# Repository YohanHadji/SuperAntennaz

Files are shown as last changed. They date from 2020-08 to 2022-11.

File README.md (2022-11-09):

# SuperAntennaz

### Introduction 

SuperAntennaz is an antenna rotator designed for satellite traking. 

It can support more than 10kg of antenna, orientate them really fast (close to 30 deg. /s) and in its final version, it is very simple to reproduce. It is therefore perfect to be built, modified, and improved by the community of space HAM enthusiasts all over the world.

### Content 
- [Specifications](#Specifications)
- [Presentation](#Presentation)
- [Part List](#Part-List)
- [Kit production and prices](#Kit-production-and-prices)

## Specifications

Max torque - Min. 60 Nm

Max speed  - 30°/s 

Weight     ~ 5.5kg

Outdorproof - YES 

## Presentation

You can vizualise the rotator in 3D online with this link : https://a360.co/2CAJL9K 

This is a render of the last version prototype :

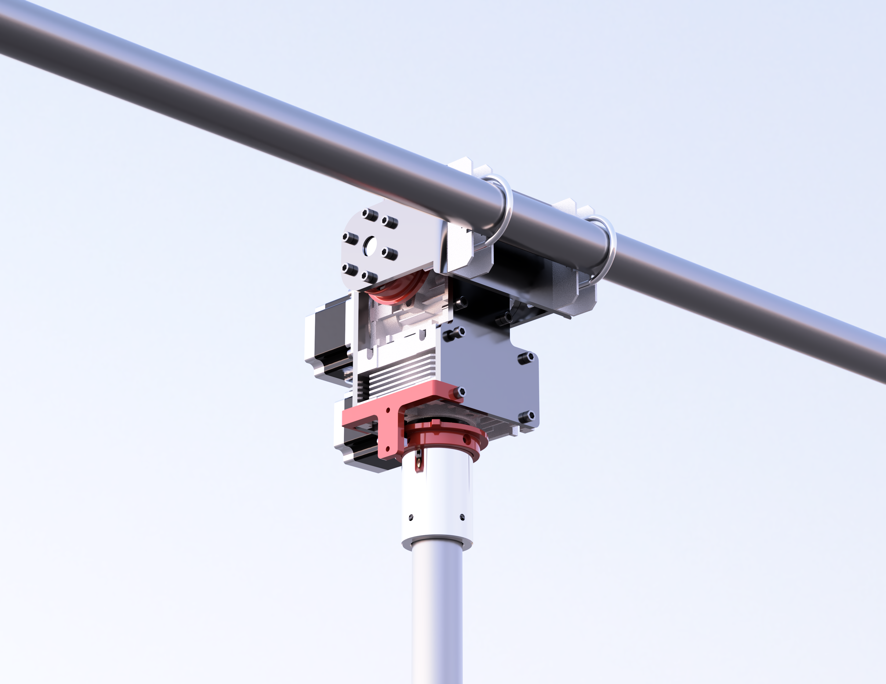
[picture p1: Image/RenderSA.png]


These are (real!) pictures of the latest version : 

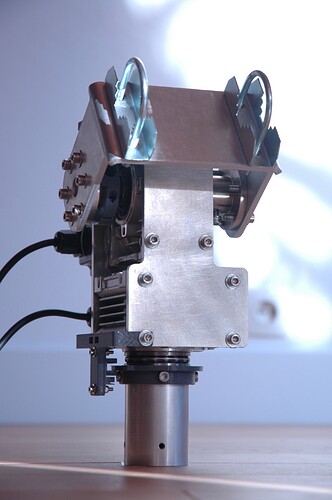
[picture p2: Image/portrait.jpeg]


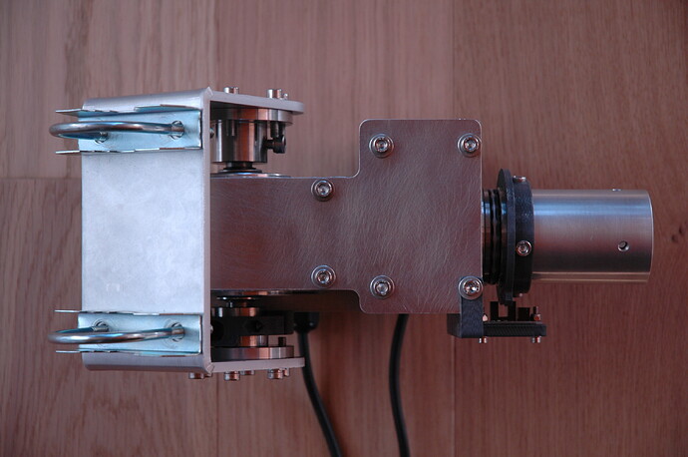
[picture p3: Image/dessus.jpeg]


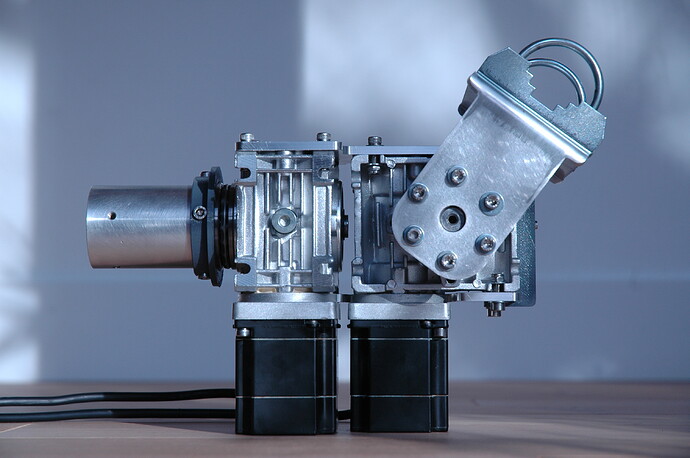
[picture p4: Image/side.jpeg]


This is a picture of a previous version of the rotator mounted on a roof with its mast, its antenna, and its creator :) 

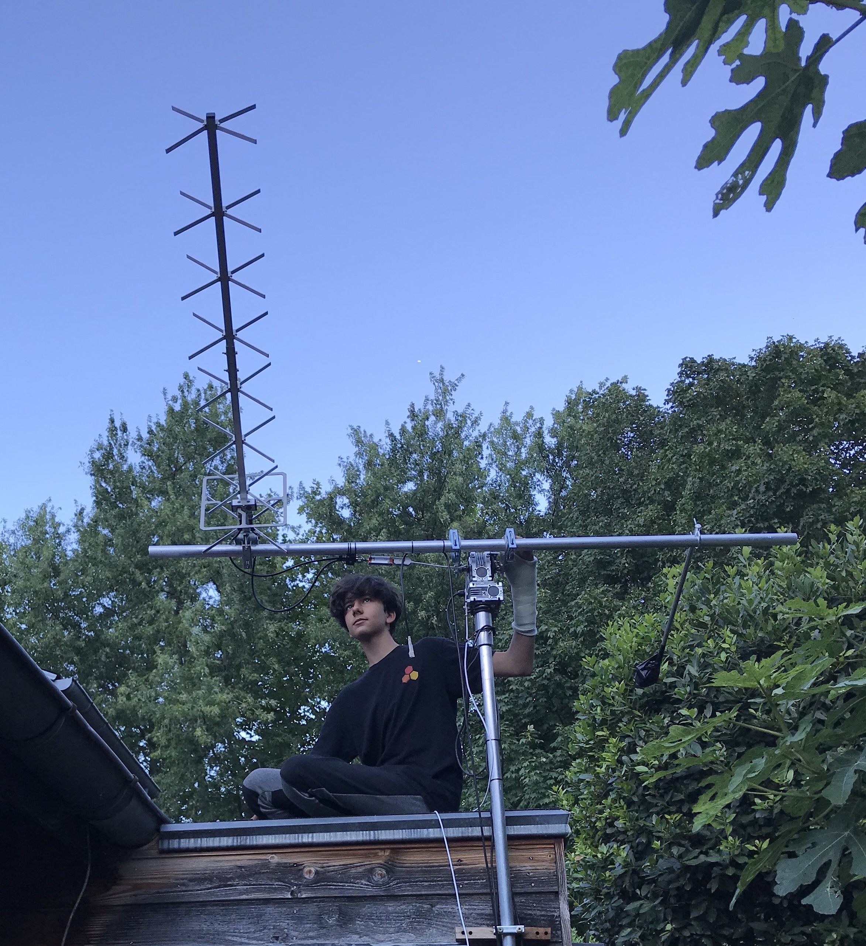
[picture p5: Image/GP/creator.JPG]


You can see the rotator in action in this video : https://www.youtube.com/watch?v=NuH7F1J6nr8

## Part List

1/ Mechanical parts on the market

- 2 * RV030 Worm Gear Reducer https://fr.aliexpress.com/item/4000405892097.html - 30€
- 2 * Reducer shaft adapatator https://fr.aliexpress.com/item/4000430356079.html - 5€
- 2 * Waterproof Stepper Motor https://www.omc-stepperonline.com/waterproof-stepper-motor/p-series-ip65-waterproof-nema-23-stepper-motor-4-0a-1-2nm-169-97oz-in.html - 80€
- 2 * 14 mm Key Hub (connection between the elevation axis and the bracket) https://ozrobotics.com/shop/14mm-stainless-steel-key-hub-18014/ - 40€
- 1 * 14 mm simple reducer shaft https://fr.aliexpress.com/item/4000378786811.html - 8€
- 1 * 14 mm double reducer shaft https://fr.aliexpress.com/item/4000378899246.html - 10€
- 2 * 50 mm mast jaws https://www.mhzshop.com/shop/Accessoires-MHz/Fixations/Brides/Bride-pour-tube-40mm.html 5€ 
- 2 * Optical Endstop - 5€ 
- ~20 * M5 screw & nut - 8€ 
- ~20 * M4 screw & nut - 8€ 

  Total = 21 parts, ~ 200€ 

2/ Machined part,(price is for part ordered one by one)

- 1 * Alumnium Mast Mount 80€
- 1 * Bracket 80€
- 1 * Reducer alumnium plate mount 30€ 

- 1 * 3D printed elevation endstop mount and pin 5€ 
- 1 * 3D printed azimuth endstop mount and pin 5€

  Sub Total = 200€ 
  
 3/ Operation Parts 

- 1 * Arduino controller ~ 20€
- 2 * Stepper Drivers ~ 100€ 
- 1 * 300W Power supply ~ 30€
- 2 * 35 mm Mast (1,5m minimum) ~ 40€ 

  Sub Total = 190€ 

Grand Total : 
~ 600 € - for a fully operational rotator 
~ 500 € - for a rotator without control electronics and mast 
       
Note : An additional cost of 100€ is to be expected for all shipping costs. 

## Kit production and prices

If you are interested by the rotator but not sure about what to buy, I could purpose the following purchase options : 

NOT-AVAILABLE RIGHT NOW - Machined parts kit, contains : Machined parts, needed screw and nuts, building instruction. - 219€ + Shipping costs (~20€ for europe)

## How to ~not~ purchase 

Kits have been available at some point in the past, but I can't find the time right now to produce some anymore. Machining prices also went high and local supplier was asking for higher order volumes. I can still try to help you at hadji.[myname]@gmail.com.

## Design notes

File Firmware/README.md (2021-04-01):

# SatNOGS Rotator Firmware for Arduino UNO/CNC Shield, for DIRECT CONNECTION TO PC via serial

Firmware [SatNOGS Rotator Controller Based on Arduino UNO and CNC V3 Shield](https://wiki.satnogs.org/SatNOGS_Arduino_Uno/CNC_Shield_Based_Rotator_Controller).

Repository includes all source files for the SatNOGS rotator controller Firmware, based on the Arduino UNO. using the CNC v3 Shield, instead of the custom SatNOGS PCB.

Electronics can be found on [satnogs-rotator-controller](https://wiki.satnogs.org/SatNOGS_Arduino_Uno/CNC_Shield_Based_Rotator_Controller)

## Instructions

In order to use this code, you need to install
 * Arduino IDE
 * [AccelStepper library](http://www.airspayce.com/mikem/arduino/AccelStepper/index.html)
 * [PID_v1 library](https://github.com/br3ttb/Arduino-PID-Library)
 * Wire library
 * Gpredict

## Easycomm implemantation

* AZ, Azimuth, number - 1 decimal place [deg]
* EL, Elevation, number - 1 decimal place [deg]
* SA, Stop azimuth moving
* SE, Stop elevation moving
* RESET, Move to home position
* PARK, Move to park position
* IP, Read an input, number
    * Temperature = 0
    * SW1 = 1
    * SW2 = 2
    * Encoder1 = 3
    * Encoder2 = 4
    * Load of M1/AZ = 5
    * Load of M2/EL = 6
    * Speed of M1/AZ (DPS) = 7
    * Speed of M2/EL (DPS) = 8
* VE, Request Version
* GS, Get status register, number
    * idle = 1
    * moving = 2
    * pointing = 4
    * error = 8
* GE, Get error register, number
    * no_error = 1
    * sensor_error = 2
    * homing_error = 4
    * motor_error = 8
    * over_temperature = 12
    * wdt_error = 16
* VL, Velocity Left ,number [mdeg/s]
* VR, Velocity Right, number [mdeg/s]
* VU, Velocity Up, number [mdeg/s]
* VD, Velocity Down, number [mdeg/s]
* CR, Read config, register [0-x]
    * Gain P for M1/AZ = 1
    * Gain I for M1/AZ = 2
    * Gain D for M1/AZ = 3
    * Gain P for M2/EL = 4
    * Gain I for M2/EL = 5
    * Gain D for M2/EL = 6
    * Azimuth park position = 7
    * Elevation park position = 8
    * Control mode (position = 0, speed = 1) = 9
* CW, Write config, register [0-x]
    * Gain P for M1/AZ = 1
    * Gain I for M1/AZ = 2
    * Gain D for M1/AZ = 3
    * Gain P for M2/EL = 4
    * Gain I for M2/EL = 5
    * Gain D for M2/EL = 6
    * Azimuth park position = 7
    * Elevation park position = 8
    * This reg is set from Vx commands control mode (position = 0, speed = 1) = 9
* RB, custom command to reboot controller

## Controller Configurations

* Stepper Motor
    * Endstops
    * Encoders, optional
    * UART or R485 (For both options the firmware is the same)

## Pins Configuration

```
   #ifndef ROTATOR_PINS_H_
   #define ROTATOR_PINS_H_
   //#define M1IN1 10 ///< Motor 1 PWM pin
   #define M1IN1 2 ///< Motor 1 PWM pin
   #define M1IN2 5  ///< Motor 1 PWM pin
   #define M1SF  7  ///< Motor 1 digital input, status flag for DC Motor Drivers
   #define M1FB  A1 ///< Motor 1 analog input, current/load feedback for DC Motor Drivers
   #define M2IN1 3 ///< Motor 2 PWM pin
   #define M2IN2 6  ///< Motor 2 PWM pin
   #define M2SF  7 ///< Motor 2 digital input, status flag for DC Motor Drivers
   #define M2FB  A0 ///< Motor 2 analog input, current/load feedback for DC Motor Drivers
   #define MOTOR_EN 8 ///< Digital output, to enable the motors
   #define SW1 11 ///< Digital input, to read the status of end-stop for motor 1
   #define SW2 9 ///< Digital input, to read the status of end-stop for motor 2
   #define RS485_DIR 2 ///< Digital output, to set the direction of RS485 communication
   #define SDA_PIN 3 ///< I2C data pin
   #define SCL_PIN 4 ///< I2C clock pin
   #define PIN12 12 ///< General purpose I/O pin
   #define PIN13 13 ///< General purpose I/O pin
   #define A2    A2 ///< General purpose I/O & analog pin
   #define A3    A3 ///< General purpose I/O & analog pin
   #endif /* ROTATOR_PINS_H_ */
```

## Testing with hamlib - rotctl or with Serial Monitor

Software to install
Final pieces to the preparation work are to install a couple of pieces of software. firstly Hamlib. This will be used to communicate between GPredict and the Arduino. Secondly we will install the main prediction software, GPredict. We will not be going into detail about setup of GPredict but assume that you have followed the installation guide and had a play around with it so you can understand what it is and how it works.

Install hamlib

Download the Hamblib software and follow the installation process. this may require you installing it with Administrator rights. using device manager find the port for the Arduino, for the purposes of this we will assume it is COM7

Using a text editor, like Notepad++, to create a file with the code below in it. Note where COM7 is and amend with your own COM port. Save as a batch file (i.e. with th extension .bat file in the same folder as rotctld (Usually found in C:\Program Files (x86)\hamlib-w64-3.2\bin )

rotctld -m 202 -r COM7 -s 9600 -T 127.0.0.1 -t 4533 -C timeout=500 -C retry=0 -vvvvvvvv > pause
Install GPredict

Download and install GPredict. Next we will need to add a rotator. Go to Edit > Preferences > Interfaces > Rotators > Add New

Give it a name. For example Arduino. The port is localhost 4533

That's it for setup. next we will test the system

Testing
We will need to do a few things to get the system running.

Start the .bat file
In GPredict open up the Antenna module and click Engage
You should see that in the batch file output a series of commands being sent to the Arduino
Check that both the Az and Ele work correctly by manually driving the rotator
Occasionally this might not work first time. A restart of both hamlib and Gpredict worked

Tweaks
There is a huge variety in parts that can get bought, here are a few tweaks that may be necessary.

Motors are turning the wrong way - This may need the pins checking

It is only moving half the distance - Change the gear ratio in the main sketch

The limit switches are not working - Change the following code in the main sketch

define DEFAULT_HOME_STATE LOW ///< Change to LOW according to Home sensor
Operation
Operating is as simple as selecting a satellite from GPredict and then selecting track. The rotator will then follow that satellite or object.f

## Contribute

The main repository lives on [Gitlab](https://gitlab.com/librespacefoundation/satnogs/satnogs-rotator-firmware) and all Merge Request should happen there.

## License



Licensed under the [GPLv3](LICENSE)

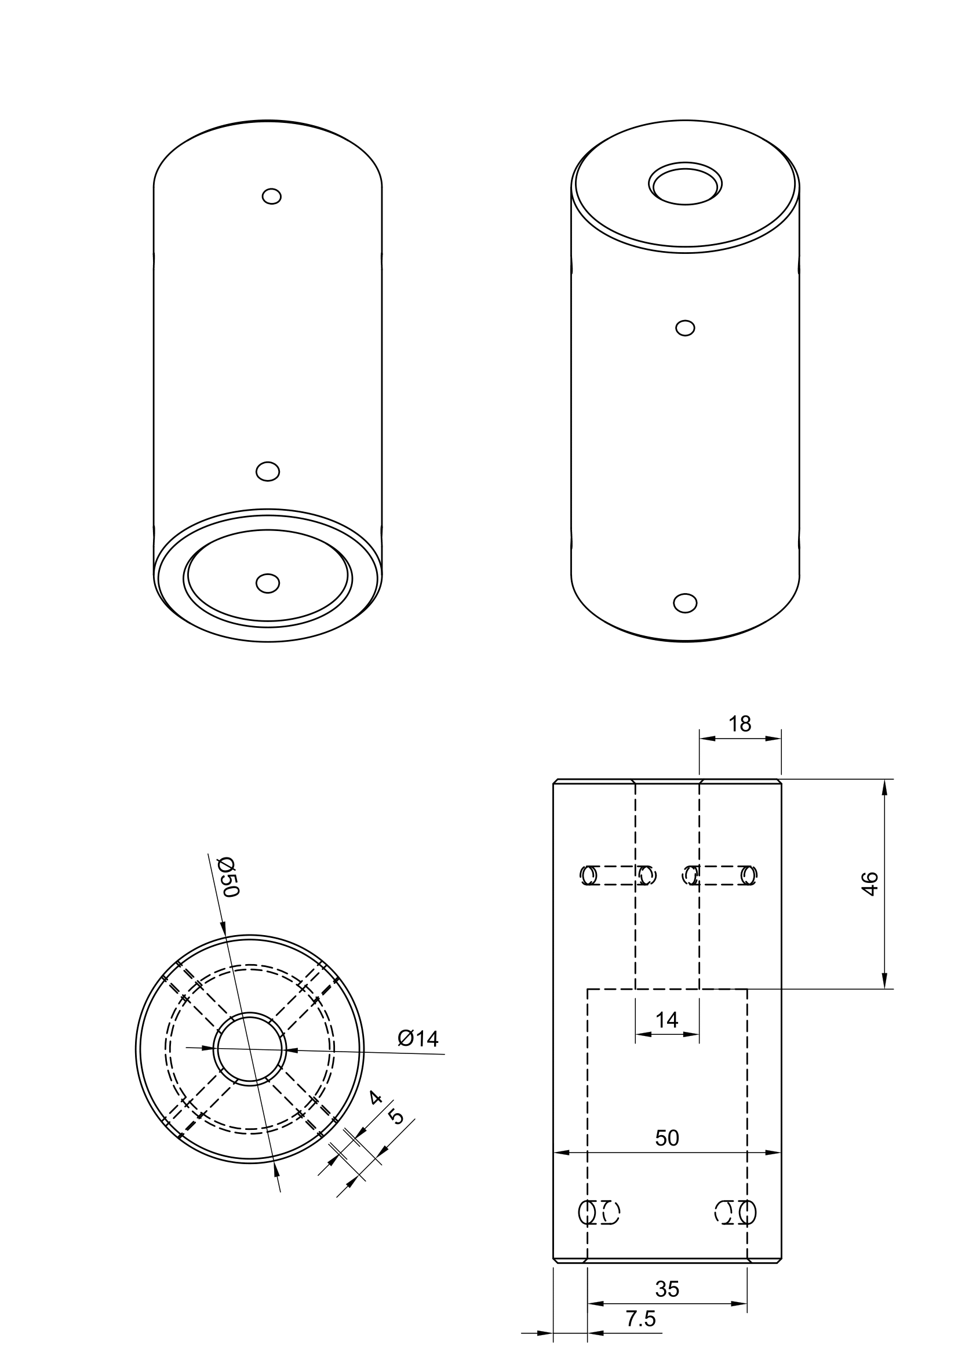
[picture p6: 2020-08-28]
Image/Fixatube-1.png

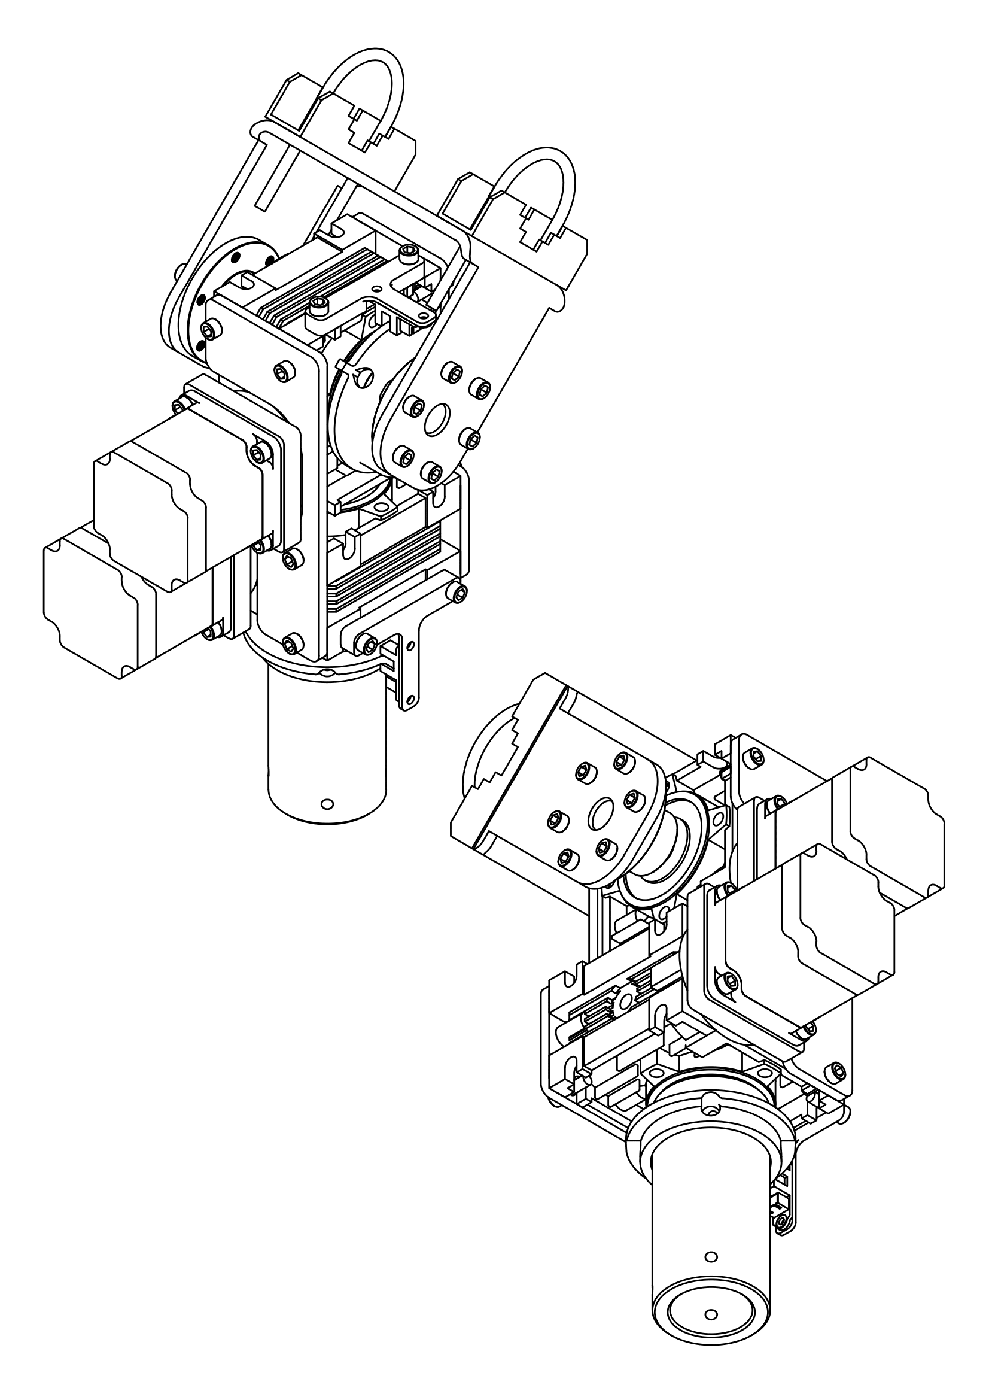
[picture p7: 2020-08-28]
Image/Blueprint-1.png

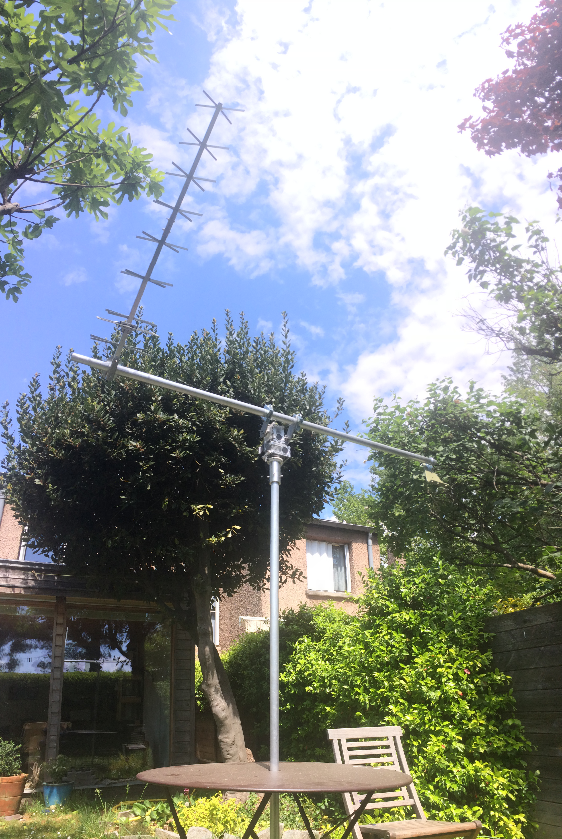
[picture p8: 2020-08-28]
Image/SAsun12.JPG

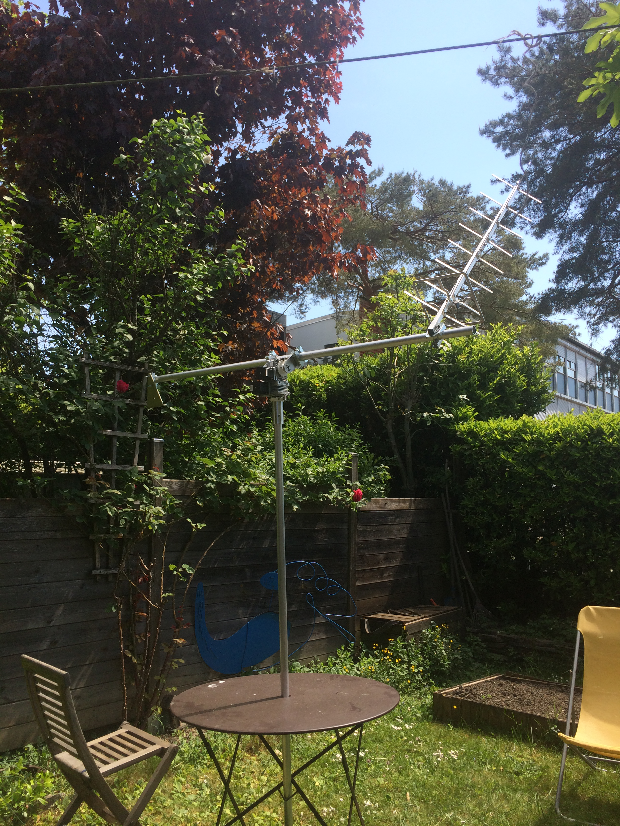
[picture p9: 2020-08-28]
Image/SAsun4.JPG

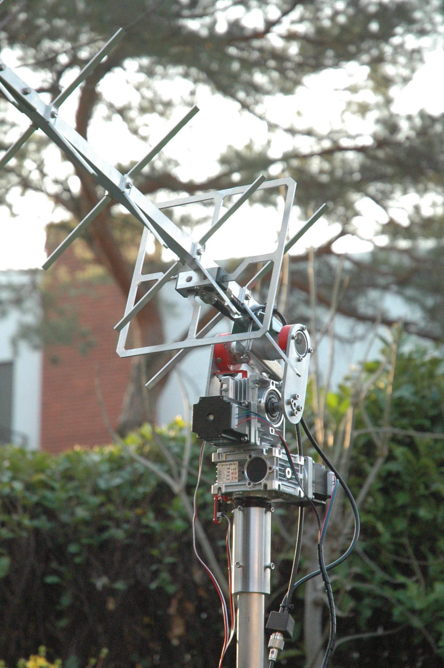
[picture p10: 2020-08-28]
Image/GP/SAV5.jpg

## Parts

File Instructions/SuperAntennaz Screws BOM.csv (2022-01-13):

Name | FIXNVIS Ref. | Qty
RONDELLE M 0 5 INOX A4 | RONM05A4 | 85
TCHC M3X25/25 INOX A4 EF DIN 912 | TCHC03/025A4EF | 4
TCHC M5X10 INOX A2 EF DIN 912 | TCHC05/010A2EF | 20
TCHC M3X12 INOX A2 EF DIN 912 | TCHC03/012A2EF | 6
TCHC M5X14 INOX A4 EF DIN 912T | CHC05/014A4EF | 10
TCHC M5X16 INOX A4 EF DIN 912 | TCHC05/016A4EF | 10
TCHC M4X20 INOX A4 EF DIN 912 | TCHC04/020A4EF | 5
TCHC M5X20 INOX A4 EF DIN 912 | TCHC05/020A4EF | 15
TCHC M5X25 INOX A4 EF DIN 912 | TCHC05/025A4EF | 2
ECROU NYLSTOP M3 INOX A2 DIN 985 | ECRNYL03A2 | 8
ECROU NYLSTOP M5 INOX A2 DIN 985 | ECRNYL05A | 45

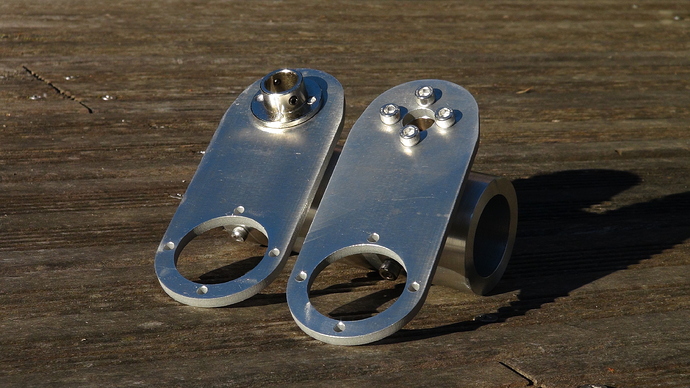
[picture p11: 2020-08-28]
Image/Parts/Part4.jpeg

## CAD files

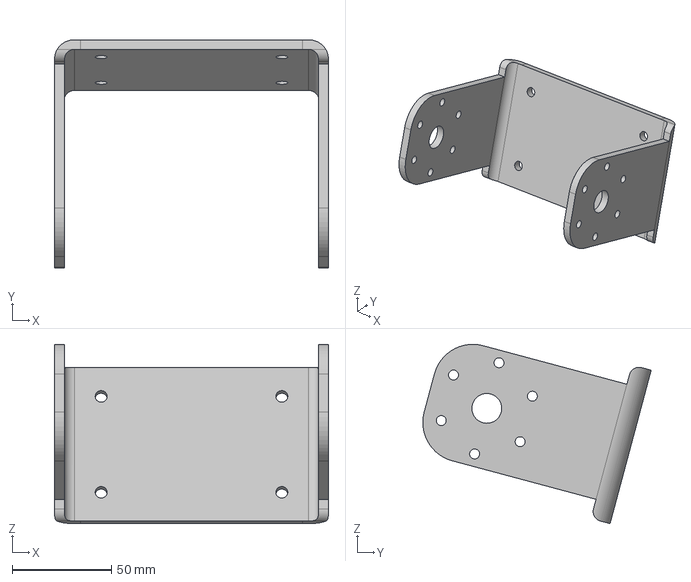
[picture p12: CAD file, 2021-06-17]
Separated Parts/V0.6/Bracket.step
138.0 x 115.0 x 90.3 mm

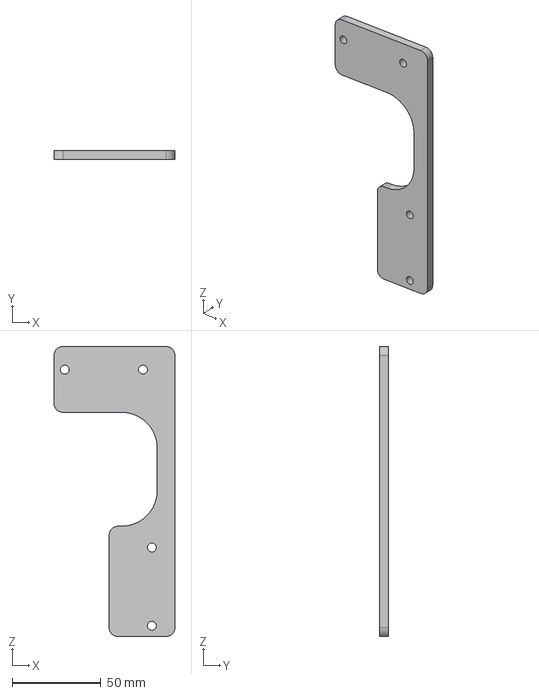
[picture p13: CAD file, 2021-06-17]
Separated Parts/V0.6/Back Plate.step
68.0 x 5.00 x 163.0 mm

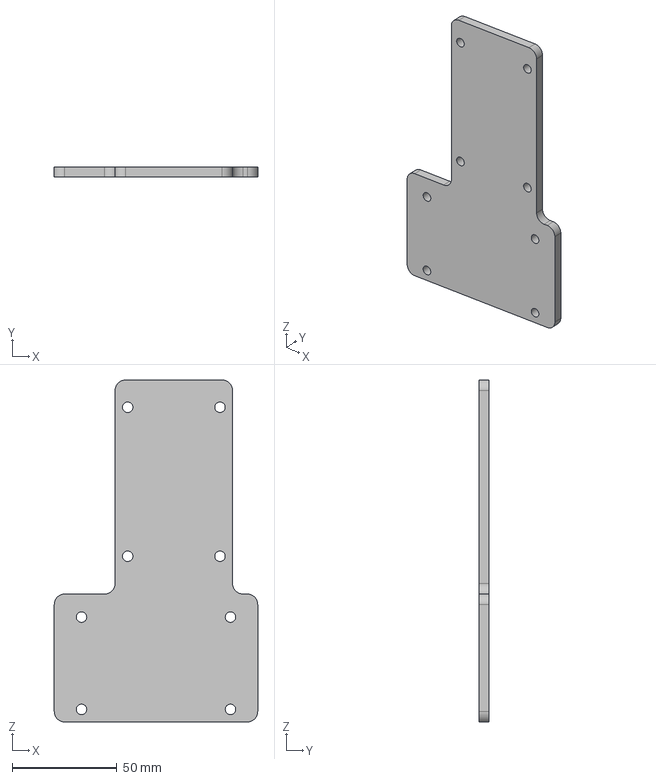
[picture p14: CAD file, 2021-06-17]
Separated Parts/V0.6/Front Plate.step
97.0 x 5.00 x 163.0 mm

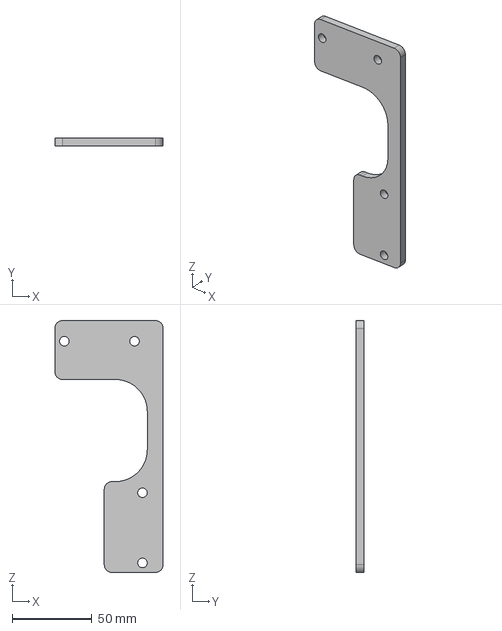
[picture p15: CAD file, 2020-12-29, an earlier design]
Separated Parts/V0.1/PlaqueBack.step
68.0 x 5.00 x 158.0 mm

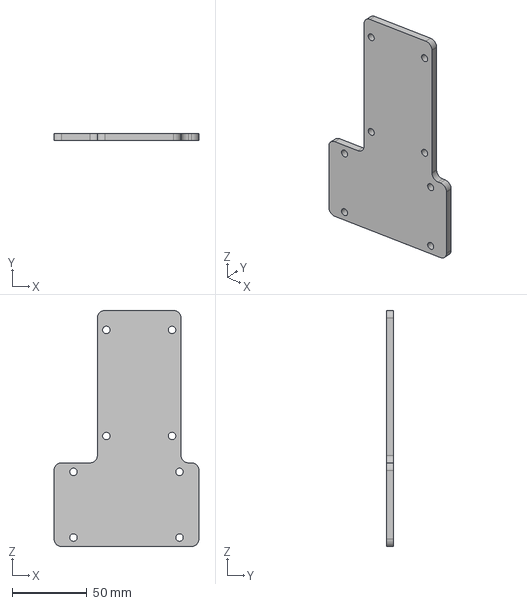
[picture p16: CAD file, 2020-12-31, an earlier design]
Separated Parts/V0.3/Front_Plate.step
97.0 x 5.00 x 158.0 mm

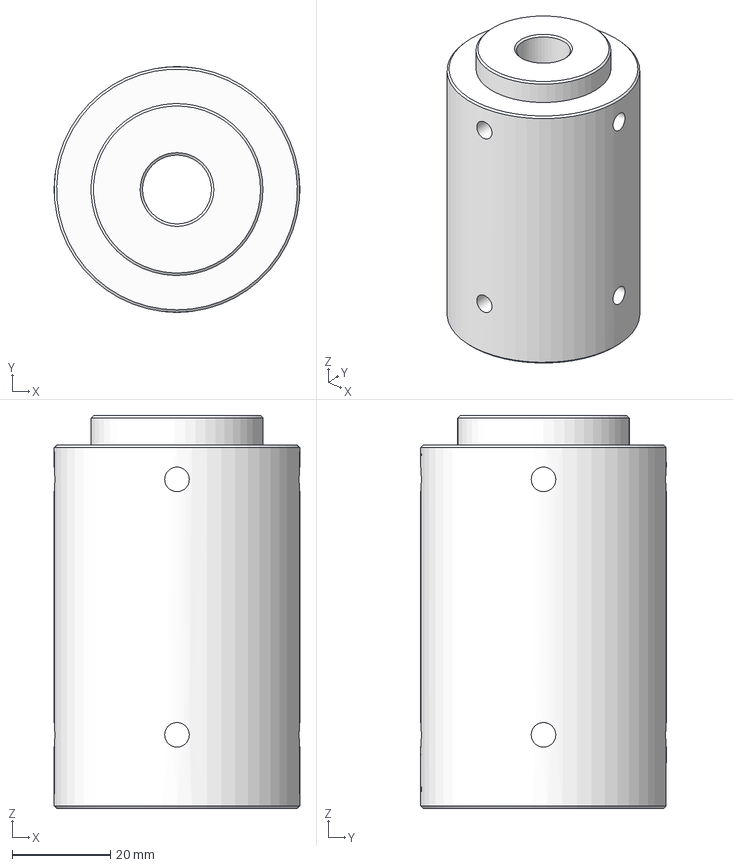
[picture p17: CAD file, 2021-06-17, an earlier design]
Separated Parts/V0.5/Fixatube.step
50.0 x 50.0 x 80.0 mm

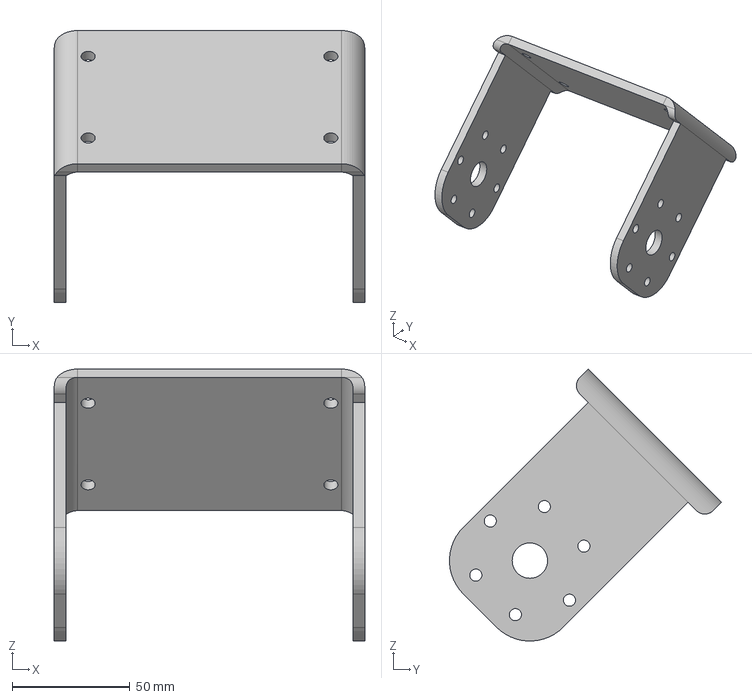
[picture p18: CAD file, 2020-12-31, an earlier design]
Separated Parts/V0.2/Bracket.step
132.0 x 115.4 x 115.4 mm

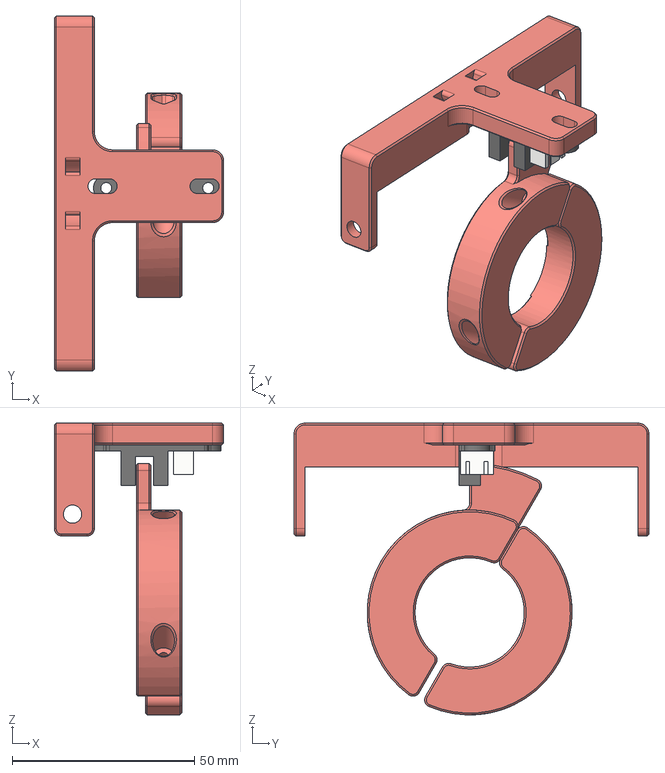
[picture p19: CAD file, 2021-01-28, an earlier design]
Separated Parts/V0.5/Endstop Elevation.step
46.5 x 97.5 x 80.1 mm
Endstop (1)
Endstop Mount (1)

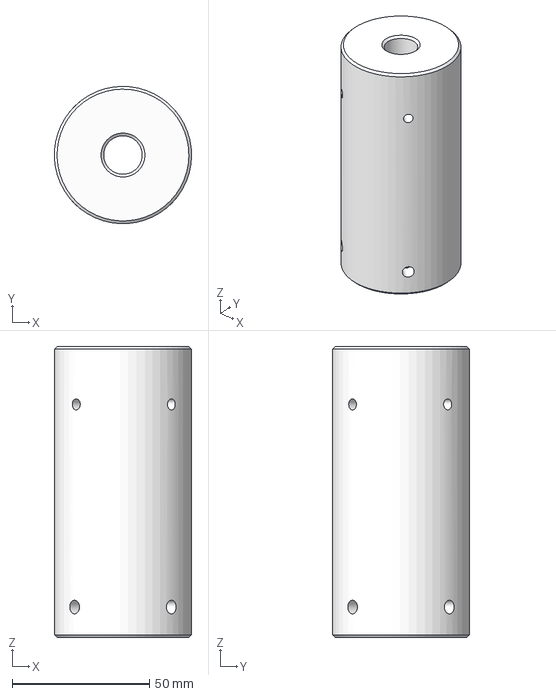
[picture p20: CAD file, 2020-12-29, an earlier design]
Separated Parts/V0.1/Fixatube.step
50.0 x 50.0 x 106.0 mm

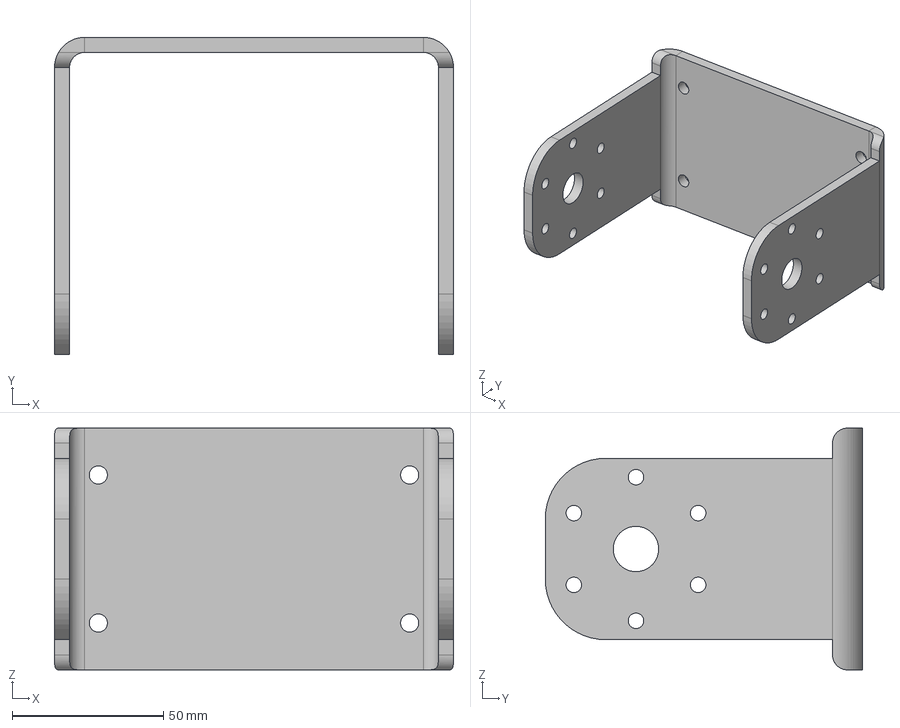
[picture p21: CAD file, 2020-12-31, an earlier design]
Separated Parts/V0.2/BracketV2.step
132.0 x 105.0 x 80.0 mm

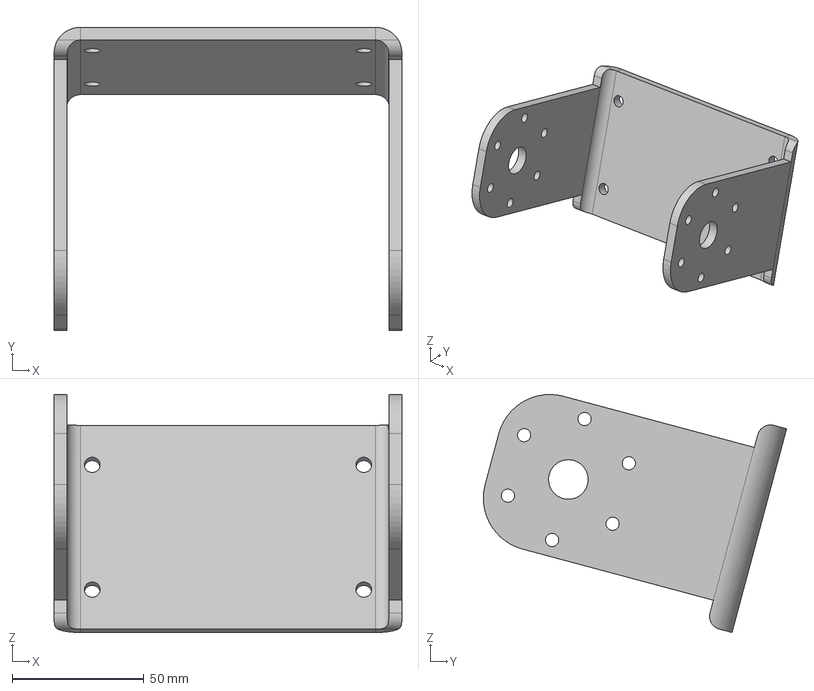
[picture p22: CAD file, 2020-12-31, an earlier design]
Separated Parts/V0.3/Bracket5mm.step
132.0 x 115.0 x 90.3 mm

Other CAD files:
Separated Parts/V0.2/Back Plate.step
Separated Parts/V0.4/Back Plate.step
Separated Parts/V0.1/PlaqueFront.step
Separated Parts/V0.3/Back_Plate.step
Separated Parts/V0.4/Bracket.step
Separated Parts/V0.4/Fixatube.step
Separated Parts/V0.5/Front Plate.step
Full Rotator/V0.1/SuperAntennazFullV0.1.f3d
Full Rotator/V0.2/SuperAntennazFullV0.2.f3d
Full Rotator/V0.3/SuperAntennazFullV0.3.f3d
Full Rotator/V0.5/SuperAntennazFullV0.5.f3d
Separated Parts/V0.1/Bracket.step
Separated Parts/V0.1/Endstop1.step
Separated Parts/V0.1/Endstop2.step
Separated Parts/V0.1/EndstopPin.step
Separated Parts/V0.1/EndstopPin1.step
Separated Parts/V0.2/Fixatube.step
Separated Parts/V0.2/Front Plate.step
Separated Parts/V0.3/Back_Plate.dxf
Separated Parts/V0.3/Fixatube.step
Separated Parts/V0.3/Front_Plate.dxf
Separated Parts/V0.4/Front Plate.f3d
Separated Parts/V0.4/Front Plate.step
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

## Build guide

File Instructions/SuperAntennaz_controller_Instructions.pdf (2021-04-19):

# SuperAntennaz controller instructions

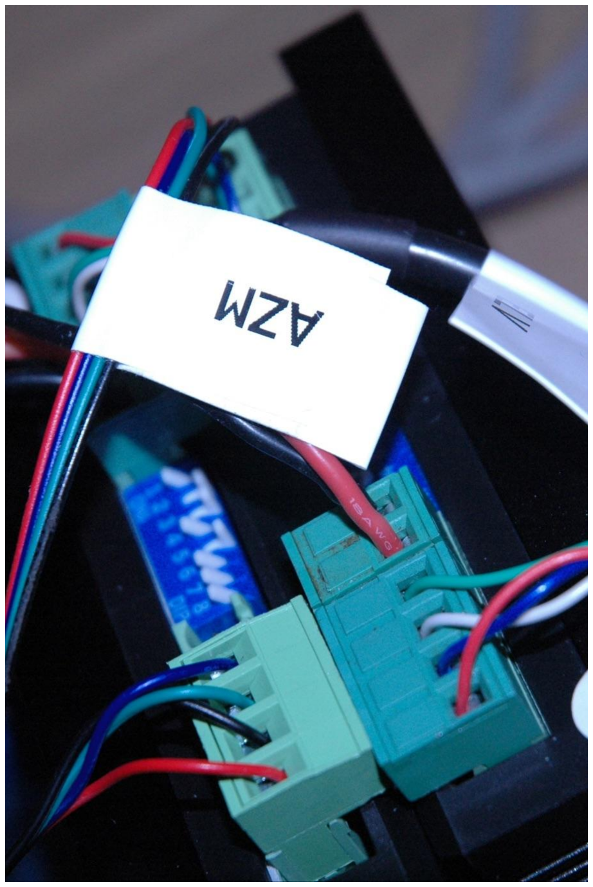
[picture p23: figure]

Thanks for purchasing your SuperAntennaz kit !

### Introduction :

This guide will help you to build your SuperAntennaz controller, you will find drawings, and advice to try to avoid the bigger mistakes you can make during the assembly.

And if you have any questions, feel free to contact me at :

hadji.yohan (at) gmail.com

### A) The parts :

Here is a short list of what you need to get a SuperAntennaz controller :

1 x Arduino UNO
3 x Nema 23 Stepper Driver
2 x Optical Endstop
1 x 36V ~300W Power supply
1 x 5V ~ 15W Power supply

You will also need enough cables to make all the wiring.

More precisely I recommend using :

Optical Endstop :
https://fr.banggood.com/3pcs-Optical-Endstop-Limit-Switch-Sensor-with-1M-3Pin-Cable-for-3D-Printer-p-1399210.html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 (https://fr.banggood.com/3pcs-Optical-Endstop-Limit-Switch-Sensor-with-1M-3Pin-Cable-for-3D-Printer-p-1399210.html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)

Stepper Drivers :

First option : high quality https://www.omc-stepperonline.com/digital-stepper-driver/digital-stepper-driver-18~56 a-20-50vdc-for-nema-23-24-34-stepper-motor-dm556t.html (https://www.omc-stepperonline.com/digital-stepper-driver/digital-stepper-driver-18~56a-20-50vdc-for-nema-23-24-34-stepper-motor-dm556t.html)

Second option : cheaper
https://fr.banggood.com/5_6A-DC-24-50V-57-or-86-2-Phase-Stepping-Driver-DM556-Stepper-Motor-Driver-Board-p-1374317.html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 (https://fr.banggood.com/5_6A-DC-24-50V-57-or-86-2-Phase-Stepping-Driver-DM556-Stepper-Motor-Driver-Board-p-1374317.html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)

Power Supply 36V :
https://www.omc-stepperonline.com/switching-power-supply/350w-36v-97a-115230v-s witching-power-supply-stepper-motor-cnc-router-kits-s-350-36.html (https://www.omc-stepperonline.com/switching-power-supply/350w-36v-97a-115230v-switching-power-supply-stepper-motor-cnc-router-kits-s-350-36.html)

Another part which is not essential but I that I highly recommend : https://www.robotshop.com/en/cytron-screw-terminal-shield-arduino.html

This will really simplify the assembly, the tests, and will avoid you to take out the soldering iron too often!

### B) The wiring

Once you have all the parts, here is a drawing of the complet wiring :

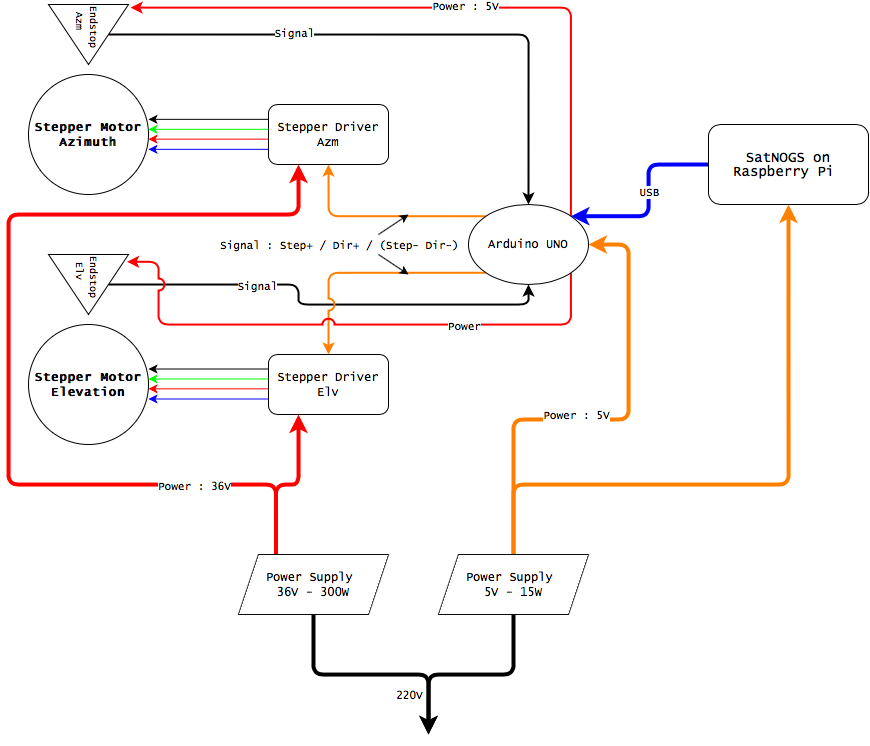
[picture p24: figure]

Please note that this is only a drawing and that some multiple wire are represented by a single one, for powering for example.

You will then want to use the arduino code provided on github : https://github.com/YohanHadji/SuperAntennaz/tree/master/Firmware

Please note this firmware is not my own, it is only a very slightly modified version of :

SatNOGS Arduino Uno/CNC Shield Based Rotator Controller
https://wiki.satnogs.org/SatNOGS_Arduino_Uno/CNC_Shield_Based_Rotator_Controller Created by the Libre Space Foundation https://libre.space

If you want to make sure you are using my modified version and not the original one, please check :

1. The name of the file you are compiling :

“satnogs_rotator_controller_modified_SuperAntennaz.ino”

2. The information provided at the beginning of the code (line 26) :
#define | RATIO | 80 | ///< Gear ratio of rotator gear box

If both are ok, then you are using the good file

What the code also tell you, is the wiring needed for the arduino :

At line 50 and 51 :

AccelStepper stepper_az(1, 3, 2);
AccelStepper stepper_el(1, 5, 4);

These two lines mean that signal lines, from the arduino to the stepper driver of the azimuth stepper (Dir+ and Step+ on the driver) should be connected to GPIO 3, and 2, on the arduino.

And the exact same thing for the elevation stepper : GPIO 5 and 4 on the arduino.

If everything is correct, GPIO 3 and 5 should both be Step+ for Azm and Elv, and GPIO 2 and 4 should both be Dir+ for Azm and Elv

Connection on driver | Azimuth | Elevation
Step+ | 3 | 5
Dir+ | 2 | 4

Step- and Dir- from each drivers are naturally connected all together to a ground point on the arduino

It is possible that Step and Dir GPIO could be inverted for each stepper on the arduino, in that case you just need to invert Step+ with Dir+ (from the same driver of course, do not invert one driver with another)

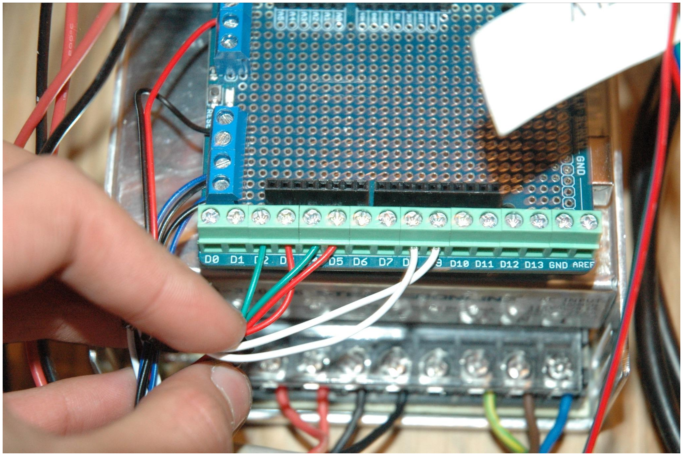
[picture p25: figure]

If you are using the arduino screw terminal shield as recommended your wiring should look a bit like this :

Each couple of one green and one red cable is a Step+ and Dir+ couple from one stepper.

On the left bottom you can see all Step- and Dir- connected together to a ground point

Now you might want to know what those white wires are : The signal wire from each optical endstop.

Again let’s take a look at the code : Line 52 endstop are declared as following :

endstop switch_az(SW1, DEFAULT_HOME_STATE), switch_el(SW2, DEFAULT_HOME_STATE);

We want to find what SW1 and SW2 mean, we can find our solution in the file :

“rotator_pins.h”

https://github.com/YohanHadji/SuperAntennaz/blob/master/Firmware/stepper_motor_controller/rotator_pins.h (https://github.com/YohanHadji/SuperAntennaz/blob/master/Firmware/stepper_motor_controller/rotator_pins.h)

Lines 26 and 27 we can find :

#define SW1 8

#define SW2 9

I recommend to always check, but SW1, so GPIO 8, should be the endstop for the Azm Driver, and SW2 so GPIO 9 on the arduino should be the endstop for the Elv Driver

Each Endstop also need to be powered with 5V from the arduino, these are the last wire on the right top you can see on the picture, connected to ground and 5V point on the arduino shield

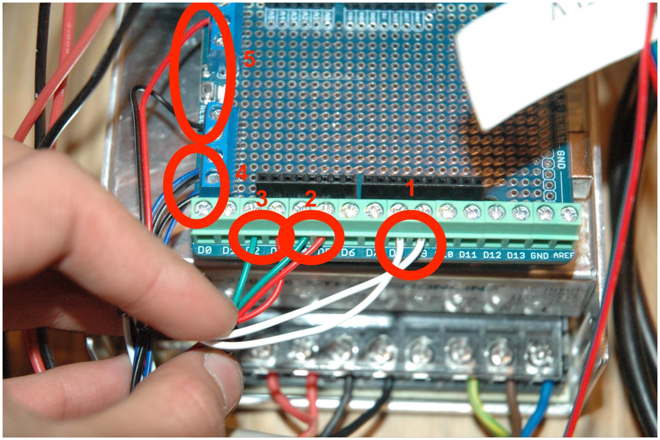
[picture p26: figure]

1 : Endstop signal, GPIO 8 = Azm, GPIO 9 = Elv
2 : Elevation driver control signal, GPIO 5 = Step+, GPIO 4 = Dir+ 3 : Azimuth driver control signal, GPIO 3 = Step+, GPIO 2 = Dir+ 4 : Dir- and Step- from each driver connected together to ground 5 : +5V and ground from arduino to optical endstop

### C) Last steps

Connecting each stepper to its driver :

There are plenty of good tutorials on youtube that will explain way better than me how to connect each of 4 wire of the stepper to its driver

Here is the datasheet of the stepper motor I recommend, you will find the wiring informations from the motor :

https://www.omc-stepperonline.com/download/23IP65-12.pdf

Connecting power supply to drivers :

Please remember that these drivers don’t have brains, so use your own, always, always, always double, or even triple check + and - polarities before powering anything!

Connecting arduino to Raspberry Pi :

Just use an USB cable

Drivers settings :

If you are using the same Stepper Motor as recommended :

https://www.omc-stepperonline.com/waterproof-stepper-motor/p-series-ip65-waterpro of-nema-23-stepper-motor-4-0a-1-2nm-169-97oz-in.html (https://www.omc-stepperonline.com/waterproof-stepper-motor/p-series-ip65-waterproof-nema-23-stepper-motor-4-0a-1-2nm-169-97oz-in.html)

The rated Current/phase is : 4.0

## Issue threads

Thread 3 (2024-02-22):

Simple reducer Ali link expired ... Found similar item on Amazon

mwfoutch, 2024-02-22:
Amazon Link below ... Confirming if it fits ... TBD

CNCTOPBAOS Output Single Shaft Diameter 14mm 0.55" Output Shaft fit for Worm Reducer Gearbox NMRV030 RV030 Nema23 Stepper Motor Length 100mm with Gaskets S Ring Corner pin https://a.co/d/fxmtajR

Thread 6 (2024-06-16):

3D print files

Joeee83, 2024-06-16:
Hi there,
i want to build the rotor for myself - is there any chance on getting access to the stls for the 3D printed endstop holders too.
vy 73

Joeee83, 2024-06-16:
My bad. I could get all out off the assembly file.

Closed 2024-06-16.

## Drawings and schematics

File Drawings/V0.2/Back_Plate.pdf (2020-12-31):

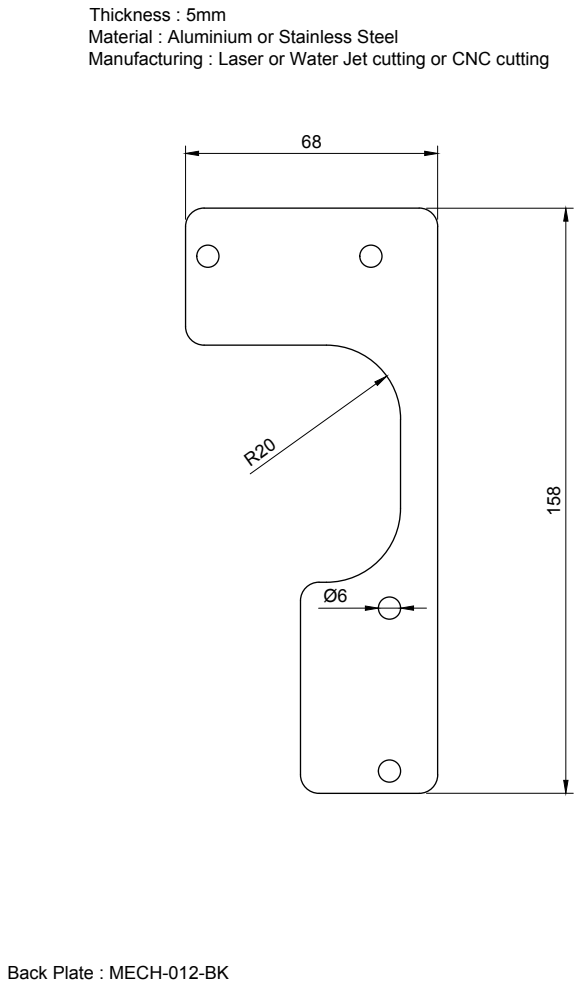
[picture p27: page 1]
Back Plate : MECH-012-BK

Thickness : 5mm
Material : Aluminium or Stainless Steel
Manufacturing : Laser or Water Jet cutting or CNC cutting

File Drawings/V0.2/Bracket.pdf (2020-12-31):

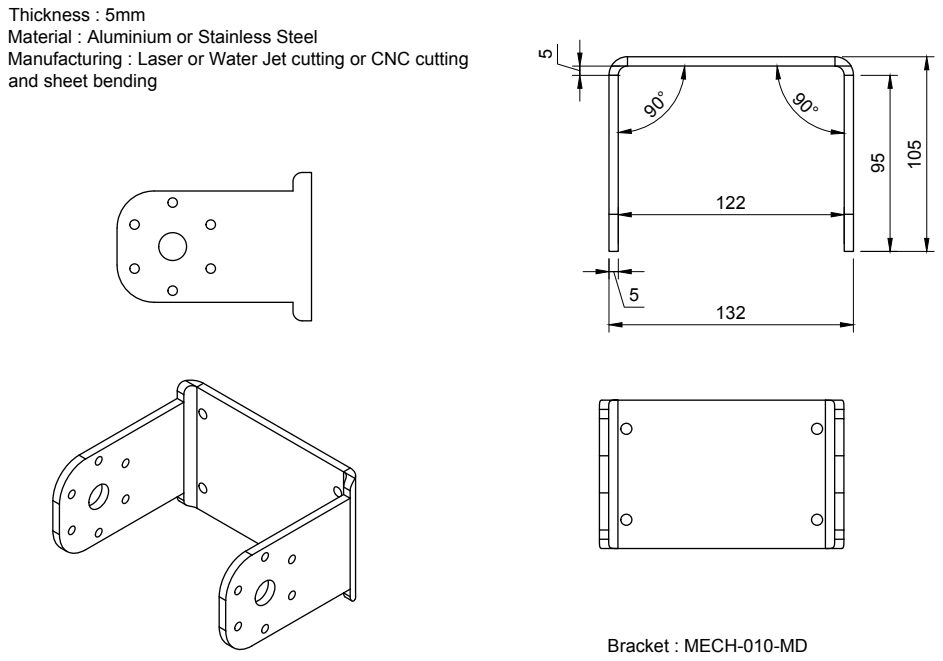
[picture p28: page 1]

Thickness : 5mm
Material : Aluminium or Stainless Steel
Manufacturing : Laser or Water Jet cutting or CNC cutting
and sheet bending

Bracket : MECH-010-MD

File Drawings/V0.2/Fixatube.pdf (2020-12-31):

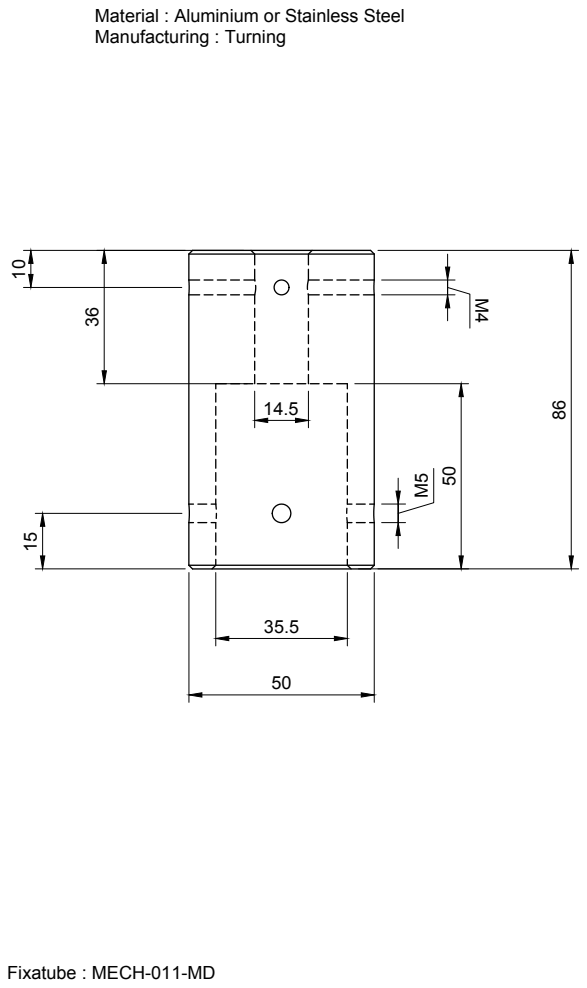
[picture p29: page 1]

Material : Aluminium or Stainless Steel
Manufacturing : Turning

Fixatube : MECH-011-MD

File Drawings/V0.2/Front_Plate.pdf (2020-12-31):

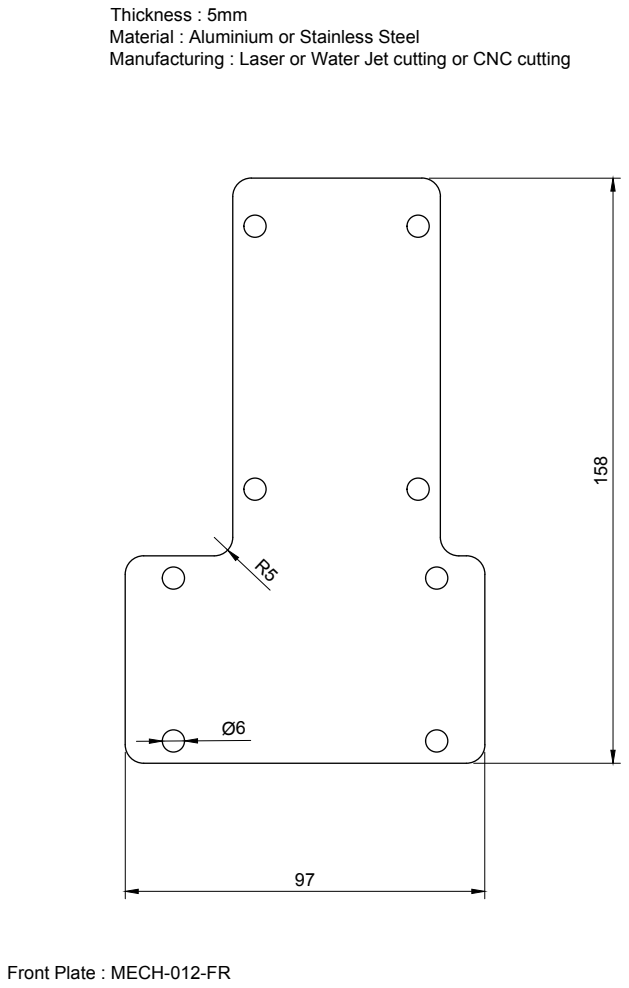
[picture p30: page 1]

Thickness : 5mm
Material : Aluminium or Stainless Steel
Manufacturing : Laser or Water Jet cutting or CNC cutting

Front Plate : MECH-012-FR

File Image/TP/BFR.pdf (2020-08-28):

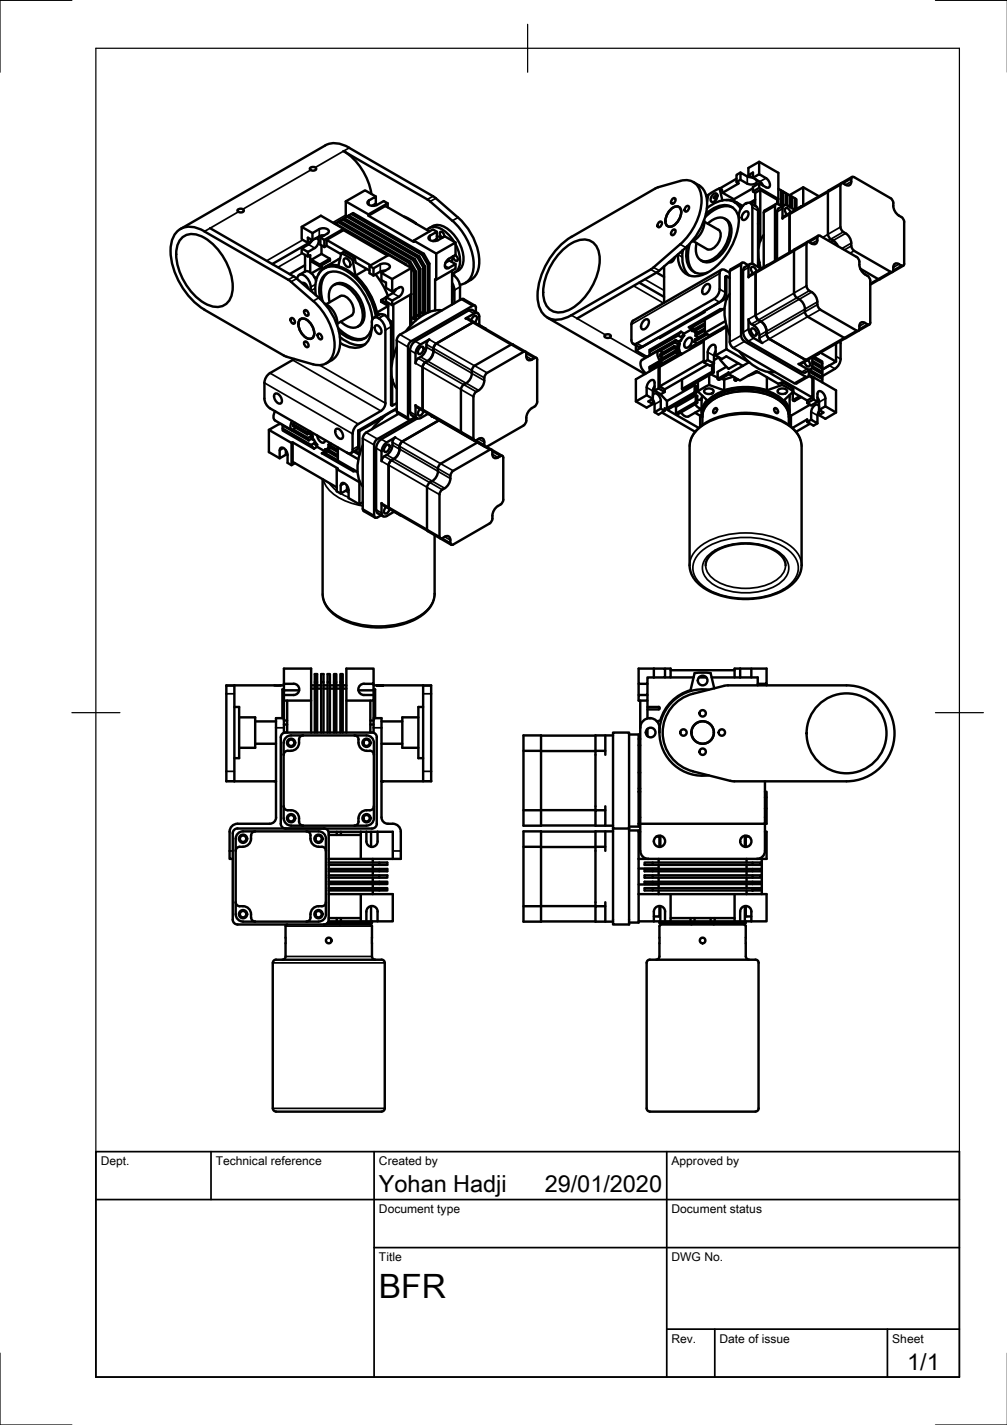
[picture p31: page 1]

Dept. | Technical reference | Created by Yohan Hadji 29/01/2020 | Approved by

Document type | Document status

Title BFR | DWG No.

Rev. | Date of issue | Sheet 1/1

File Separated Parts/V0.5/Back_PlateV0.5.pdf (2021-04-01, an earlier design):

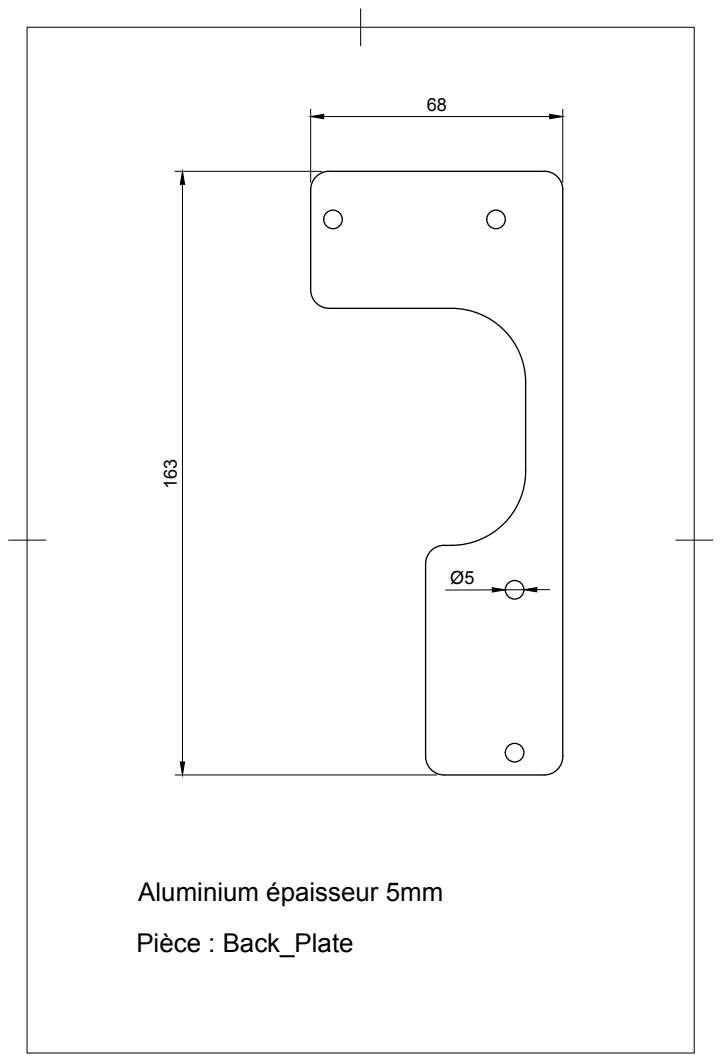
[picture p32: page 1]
Aluminium épaisseur 5mm; Pièce : Back_Plate

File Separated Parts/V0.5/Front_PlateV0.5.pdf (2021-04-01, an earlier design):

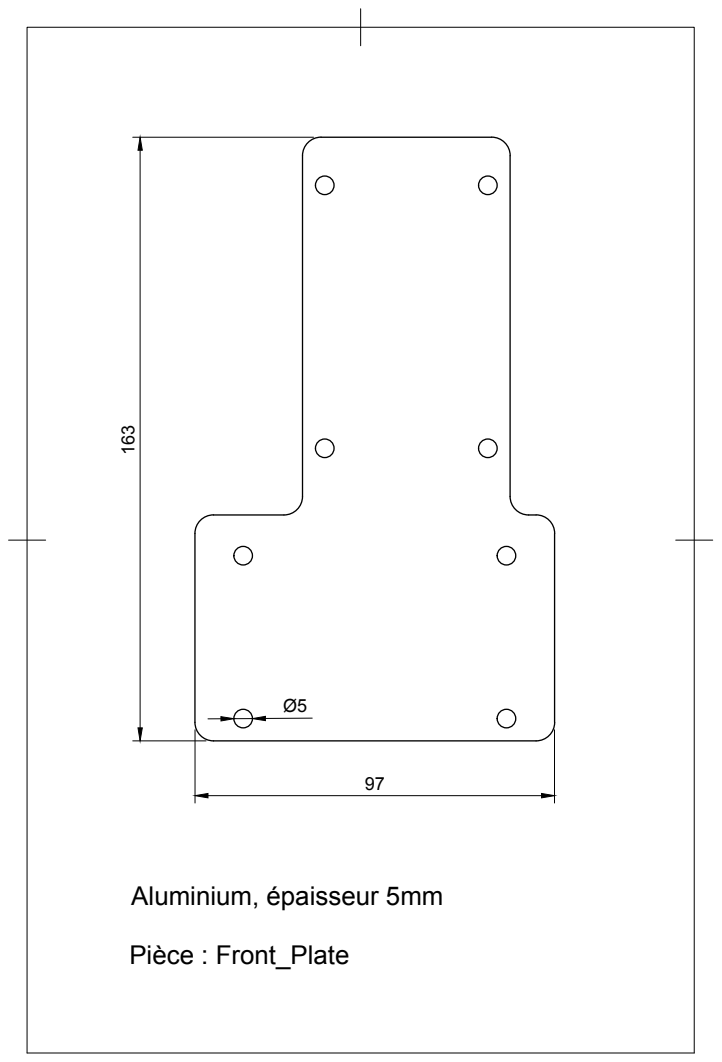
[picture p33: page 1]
Aluminium, épaisseur 5mm; Pièce : Front_Plate

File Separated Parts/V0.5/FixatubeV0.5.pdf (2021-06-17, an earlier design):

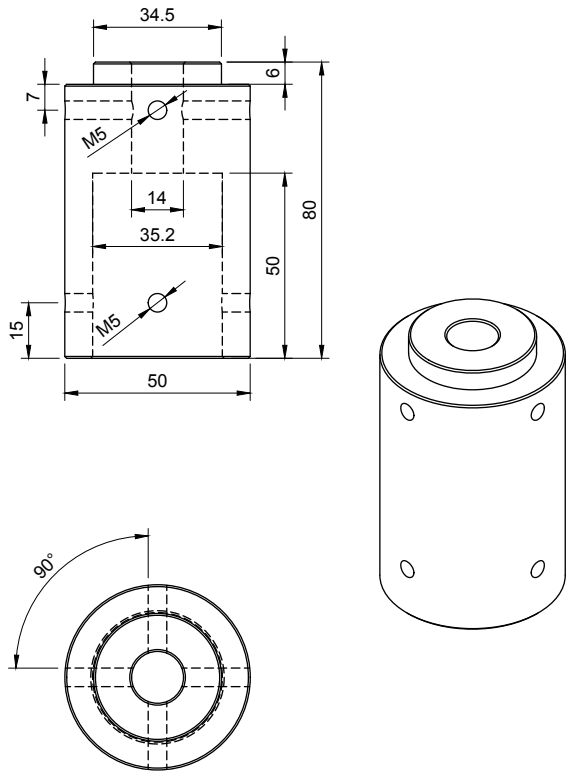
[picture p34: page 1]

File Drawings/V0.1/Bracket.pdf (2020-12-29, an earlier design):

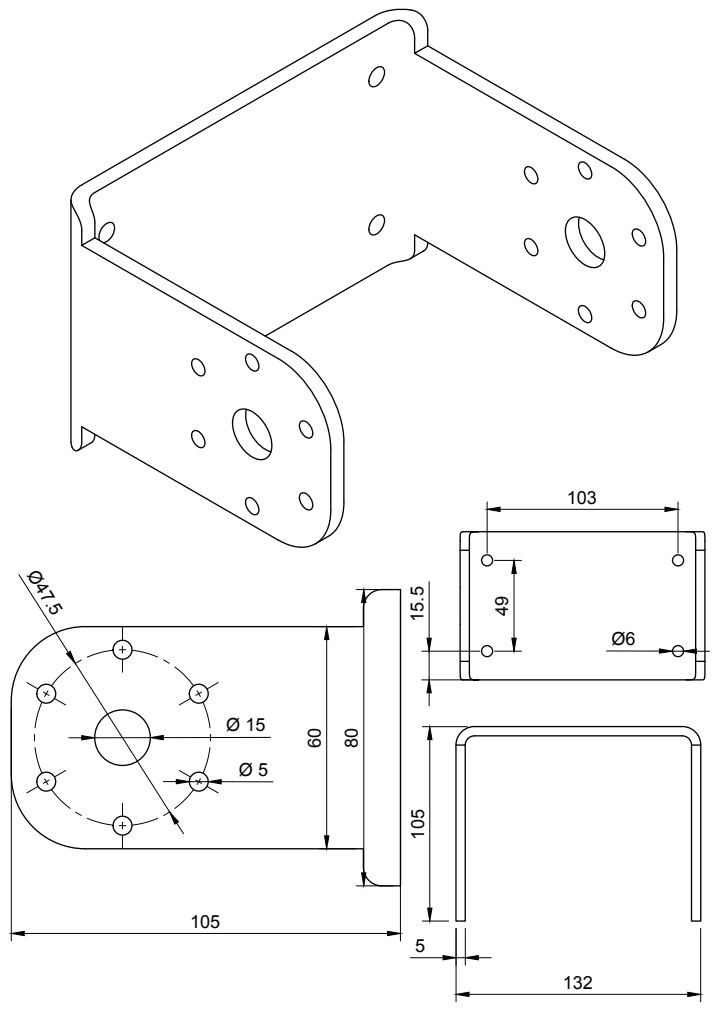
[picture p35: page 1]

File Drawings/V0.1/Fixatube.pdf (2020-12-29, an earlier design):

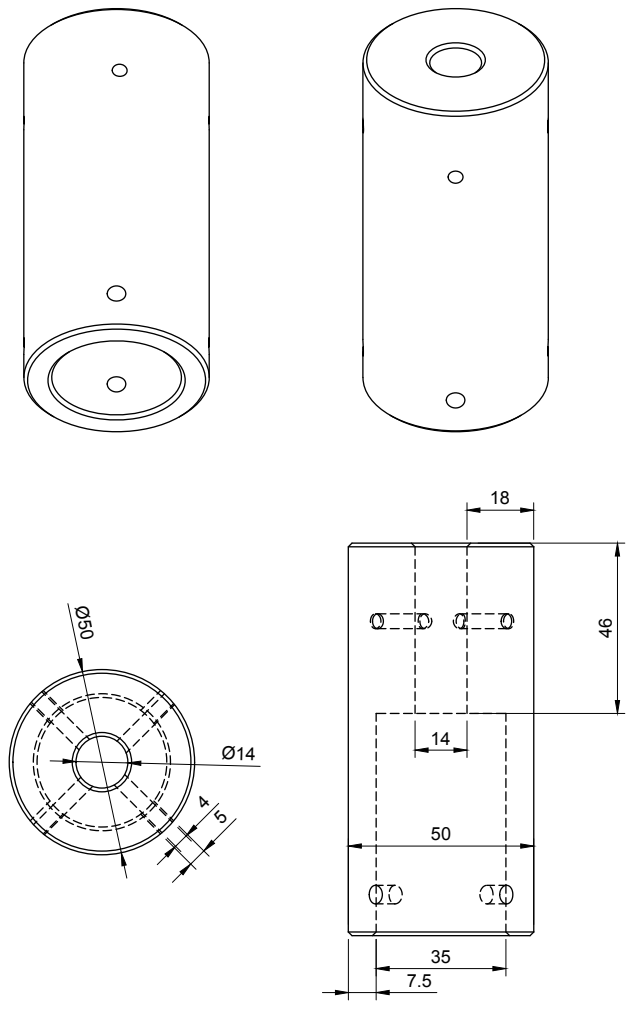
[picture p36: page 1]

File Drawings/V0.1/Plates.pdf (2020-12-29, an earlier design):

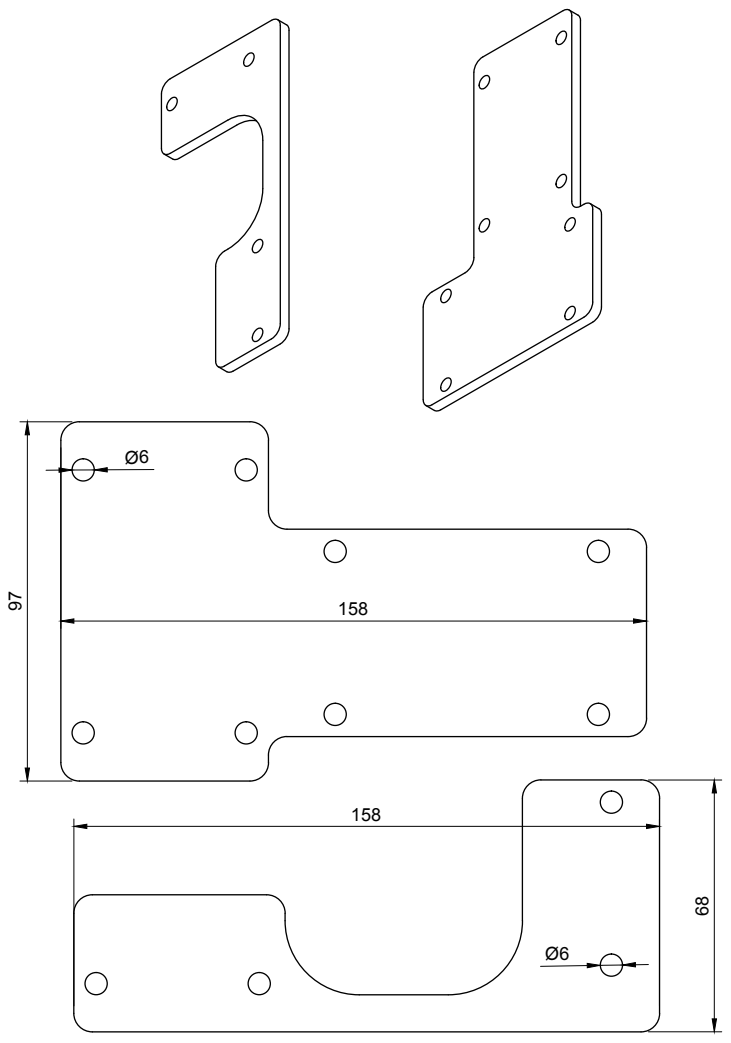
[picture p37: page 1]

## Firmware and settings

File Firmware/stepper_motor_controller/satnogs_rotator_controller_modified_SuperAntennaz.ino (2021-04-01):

/*!
 * @file stepper_motor_controller.ino
 *
 * This is the documentation for satnogs rotator controller firmware
 * for stepper motors configuration. The board (PCB) is placed in
 * <a href="https://gitlab.com/librespacefoundation/satnogs/satnogs-rotator-controller">
 * satnogs-rotator-controller </a> and is for releases:
 * v2.0
 * v2.1
 * v2.2
 * <a href="https://wiki.satnogs.org/SatNOGS_Rotator_Controller"> wiki page </a>
 *
 * @section dependencies Dependencies
 *
 * This firmware depends on <a href="http://www.airspayce.com/mikem/arduino/AccelStepper/index.htmlhttp://www.airspayce.com/mikem/arduino/AccelStepper/index.html">
 * AccelStepper library</a> being present on your system. Please make sure you
 * have installed the latest version before using this firmware.
 *
 * @section license License
 *
 * Licensed under the GPLv3.
 *
 */

#define SAMPLE_TIME        0.1   ///< Control loop in s
#define RATIO              80    ///< Gear ratio of rotator gear box                                 default 54
#define MICROSTEP          2     ///< Set Microstep
#define MIN_PULSE_WIDTH    20    ///< In microsecond for AccelStepper
#define MAX_SPEED          1600  ///< In steps/s, consider the microstep
#define MAX_ACCELERATION   1600  ///< In steps/s^2, consider the microstep
#define SPR                400L ///< Step Per Revolution, consider the microstep
#define MIN_M1_ANGLE       0     ///< Minimum angle of azimuth
#define MAX_M1_ANGLE       360   ///< Maximum angle of azimuth
#define MIN_M2_ANGLE       0     ///< Minimum angle of elevation
#define MAX_M2_ANGLE       180   ///< Maximum angle of elevation
#define DEFAULT_HOME_STATE HIGH  ///< Change to LOW according to Home sensor
#define HOME_DELAY         12000 ///< Time for homing Deceleration in millisecond

#include <AccelStepper.h>
#include <Wire.h>
//#include <globals.h>
#include "easycomm.h"
#include "rotator_pins.h"
//#include <rs485.h>
#include "endstop.h"
//#include <watchdog.h>

uint32_t t_run = 0; // run time of uC
easycomm comm;
AccelStepper stepper_az(1, 3, 2);
AccelStepper stepper_el(1, 5, 4);
endstop switch_az(SW1, DEFAULT_HOME_STATE), switch_el(SW2, DEFAULT_HOME_STATE);
//wdt_timer wdt;

enum _rotator_error homing(int32_t seek_az, int32_t seek_el);
int32_t deg2step(float deg);
float step2deg(int32_t step);

void setup() {
    // Homing switch
    switch_az.init();
    switch_el.init();

    // Serial Communication
    comm.easycomm_init();

    // Stepper Motor setup
    stepper_az.setEnablePin(MOTOR_EN);
    stepper_az.setPinsInverted(false, false, true);
    stepper_az.enableOutputs();
    stepper_az.setMaxSpeed(MAX_SPEED);
    stepper_az.setAcceleration(MAX_ACCELERATION);
    stepper_az.setMinPulseWidth(MIN_PULSE_WIDTH);
    stepper_el.setPinsInverted(false, false, true);
    stepper_el.enableOutputs();
    stepper_el.setMaxSpeed(MAX_SPEED);
    stepper_el.setAcceleration(MAX_ACCELERATION);
    stepper_el.setMinPulseWidth(MIN_PULSE_WIDTH);

    // Initialize WDT
   // wdt.watchdog_init();
}

void loop() {
    // Update WDT
   // wdt.watchdog_reset();

    // Get end stop status
    rotator.switch_az = switch_az.get_state();
    rotator.switch_el = switch_el.get_state();

    // Run easycomm implementation
    comm.easycomm_proc();

    // Get position of both axis
    control_az.input = step2deg(stepper_az.currentPosition());
    control_el.input = step2deg(stepper_el.currentPosition());

    // Check rotator status
    if (rotator.rotator_status != error) {
        if (rotator.homing_flag == false) {
            // Check home flag
            rotator.control_mode = position;
            // Homing
            rotator.rotator_error = homing(deg2step(-MAX_M1_ANGLE),
                                           deg2step(-MAX_M2_ANGLE));
            if (rotator.rotator_error == no_error) {
                // No error
                rotator.rotator_status = idle;
                rotator.homing_flag = true;
            } else {
                // Error
                rotator.rotator_status = error;
                rotator.rotator_error = homing_error;
            }
        } else {
            // Control Loop
            stepper_az.moveTo(deg2step(control_az.setpoint));
            stepper_el.moveTo(deg2step(control_el.setpoint));
            rotator.rotator_status = pointing;
            // Move azimuth and elevation motors
            stepper_az.run();
            stepper_el.run();
            // Idle rotator
            if (stepper_az.distanceToGo() == 0 && stepper_el.distanceToGo() == 0) {
                rotator.rotator_status = idle;
            }
        }
    } else {
        // Error handler, stop motors and disable the motor driver
        stepper_az.stop();
        stepper_az.disableOutputs();
        stepper_el.stop();
        stepper_el.disableOutputs();
        if (rotator.rotator_error != homing_error) {
            // Reset error according to error value
            rotator.rotator_error = no_error;
            rotator.rotator_status = idle;
        }
    }
}

/**************************************************************************/
/*!
    @brief    Move both axis with one direction in order to find home position,
              end-stop switches
    @param    seek_az
              Steps to find home position for azimuth axis
    @param    seek_el
              Steps to find home position for elevation axis
    @return   _rotator_error
*/
/**************************************************************************/
enum _rotator_error homing(int32_t seek_az, int32_t seek_el) {
    bool isHome_az = false;
    bool isHome_el = false;

    // Move motors to "seek" position
    stepper_az.moveTo(seek_az);
    stepper_el.moveTo(seek_el);

    // Homing loop
    while (isHome_az == false || isHome_el == false) {
        // Update WDT
       // wdt.watchdog_reset();
        if (switch_az.get_state() == true && !isHome_az) {
            // Find azimuth home
            stepper_az.moveTo(stepper_az.currentPosition());
            isHome_az = true;
        }
        if (switch_el.get_state() == true && !isHome_el) {
            // Find elevation home
            stepper_el.moveTo(stepper_el.currentPosition());
            isHome_el = true;
        }
        // Check if the rotator goes out of limits or something goes wrong (in
        // mechanical)
        if ((stepper_az.distanceToGo() == 0 && !isHome_az) ||
            (stepper_el.distanceToGo() == 0 && !isHome_el)){
            return homing_error;
        }
        // Move motors to "seek" position
        stepper_az.run();
        stepper_el.run();
    }
    // Delay to Deccelerate and homing, to complete the movements
    uint32_t time = millis();
    while (millis() - time < HOME_DELAY) {
       // wdt.watchdog_reset();
        stepper_az.run();
        stepper_el.run();
    }
    // Set the home position and reset all critical control variables
    stepper_az.setCurrentPosition(0);
    stepper_el.setCurrentPosition(0);
    control_az.setpoint = 0;
    control_el.setpoint = 0;

    return no_error;
}

/**************************************************************************/
/*!
    @brief    Convert degrees to steps according to step/revolution, rotator
              gear box ratio and microstep
    @param    deg
              Degrees in float format
    @return   Steps for stepper motor driver, int32_t
*/
/**************************************************************************/
int32_t deg2step(float deg) {
    return (RATIO * SPR * deg / 360);
}

/**************************************************************************/
/*!
    @brief    Convert steps to degrees according to step/revolution, rotator
              gear box ratio and microstep
    @param    step
              Steps in int32_t format
    @return   Degrees in float format
*/
/**************************************************************************/
float step2deg(int32_t step) {
    return (360.00 * step / (SPR * RATIO));
}

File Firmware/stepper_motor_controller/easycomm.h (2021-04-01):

/*!
* @file easycomm.h
*
* It is a driver for easycomm 3 protocol as referred, in Hamlib.
*
* Licensed under the GPLv3
*
*/

#ifndef LIBRARIES_EASYCOMM_H_
#define LIBRARIES_EASYCOMM_H_

#include <Arduino.h>
#include <WString.h>
#include <avr/wdt.h>
//#include "rs485.h"
#include "rotator_pins.h"
#include "globals.h"

#define RS485_TX_TIME 9     ///< Delay "t"ms to write in serial for RS485 implementation
#define BUFFER_SIZE   256   ///< Set the size of serial buffer
#define BAUDRATE      19200 ///< Set the Baudrate of easycomm 3 protocol

//rs485 rs485(RS485_DIR, RS485_TX_TIME);

/**************************************************************************/
/*!
    @brief    Class that functions for easycomm 3 implementation
*/
/**************************************************************************/
class easycomm {
public:

    /**************************************************************************/
    /*!
        @brief    Initialize the RS485 bus
    */
    /**************************************************************************/
    void easycomm_init() {
       // rs485.begin(BAUDRATE);
	    Serial.begin(9600);
    }

    /**************************************************************************/
    /*!
        @brief    Get the commands from RS485 and response to the client
    */
    /**************************************************************************/
    void easycomm_proc() {
        char buffer[BUFFER_SIZE];
        char incomingByte;
        char *Data = buffer;
        char *rawData;
        static uint16_t BufferCnt = 0;
        char data[100];
        String str1, str2, str3, str4, str5, str6;

        // Read from serial
        while (Serial.available() > 0) {
            incomingByte = Serial.read();

            // Read new data, '\n' means new pacakage
            if (incomingByte == '\n' || incomingByte == '\r') {
                buffer[BufferCnt] = 0;
                if (buffer[0] == 'A' && buffer[1] == 'Z') {
                    if (buffer[2] == ' ' && buffer[3] == 'E' &&
                        buffer[4] == 'L') {
                        // Send current absolute position in deg
                        str1 = String("AZ");
                        str2 = String(control_az.input, 1);
                        str3 = String(" EL");
                        str4 = String(control_el.input, 1);
                        str5 = String("\n");
                        Serial.print(str1 + str2 + str3 + str4 + str5);
                    } else {
                        // Get the absolute position in deg for azimuth
                        rotator.control_mode = position;
                        rawData = strtok_r(Data, " ", &Data);
                        strncpy(data, rawData + 2, 10);
                        if (isNumber(data)) {
                            control_az.setpoint = atof(data);
                        }
                        // Get the absolute position in deg for elevation
                        rawData = strtok_r(Data, " ", &Data);
                        if (rawData[0] == 'E' && rawData[1] == 'L') {
                            strncpy(data, rawData + 2, 10);
                            if (isNumber(data)) {
                                control_el.setpoint = atof(data);
                            }
                        }
                    }
                } else if (buffer[0] == 'E' && buffer[1] == 'L') {
                        // Get the absolute position in deg for elevation
                        rotator.control_mode = position;
                        rawData = strtok_r(Data, " ", &Data);
                        if (rawData[0] == 'E' && rawData[1] == 'L') {
                            strncpy(data, rawData + 2, 10);
                            if (isNumber(data)) {
                                control_el.setpoint = atof(data);
                            }
                        }
                } else if (buffer[0] == 'V' && buffer[1] == 'U') {
                    // Elevation increase speed in mdeg/s
                    rotator.control_mode = speed;
                    strncpy(data, Data + 2, 10);
                    if (isNumber(data)) {
                        // Convert to deg/s
                        control_el.setpoint_speed = atof(data) / 1000;
                    }
                } else if (buffer[0] == 'V' && buffer[1] == 'D') {
                    // Elevation decrease speed in mdeg/s
                    rotator.control_mode = speed;
                    strncpy(data, Data + 2, 10);
                    if (isNumber(data)) {
                        // Convert to deg/s
                        control_el.setpoint_speed = - atof(data) / 1000;
                    }
                } else if (buffer[0] == 'V' && buffer[1] == 'L') {
                    // Azimuth increase speed in mdeg/s
                    rotator.control_mode = speed;
                    strncpy(data, Data + 2, 10);
                    if (isNumber(data)) {
                        // Convert to deg/s
                        control_az.setpoint_speed = atof(data) / 1000;
                    }
                } else if (buffer[0] == 'V' && buffer[1] == 'R') {
                    // Azimuth decrease speed in mdeg/s
                    rotator.control_mode = speed;
                    strncpy(data, Data + 2, 10);
                    if (isNumber(data)) {
                        // Convert to deg/s
                        control_az.setpoint_speed = - atof(data) / 1000;
                    }
                } else if (buffer[0] == 'S' && buffer[1] == 'A' &&
                           buffer[2] == ' ' && buffer[3] == 'S' &&
                           buffer[4] == 'E') {
                    // Stop Moving
                    rotator.control_mode = position;
                    str1 = String("AZ");
                    str2 = String(control_az.input, 1);
                    str3 = String(" EL");
                    str4 = String(control_el.input, 1);
                    str5 = String("\n");
                    Serial.print(str1 + str2 + str3 + str4 + str5);
                    control_az.setpoint = control_az.input;
                    control_el.setpoint = control_el.input;
                } else if (buffer[0] == 'R' && buffer[1] == 'E' &&
                           buffer[2] == 'S' && buffer[3] == 'E' &&
                           buffer[4] == 'T') {
                    // Reset the rotator, go to home position
                    str1 = String("AZ");
                    str2 = String(control_az.input, 1);
                    str3 = String(" EL");
                    str4 = String(control_el.input, 1);
                    str5 = String("\n");
                    Serial.print(str1 + str2 + str3 + str4 + str5);
                    rotator.homing_flag = false;
                } else if (buffer[0] == 'P' && buffer[1] == 'A' &&
                           buffer[2] == 'R' && buffer[3] == 'K' ) {
                    // Park the rotator
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

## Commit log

2020-12-29 Adding folder
    [BracketVF.step, Endstop1VF.step, Endstop2VF.step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]
2020-12-29 Name change
    [EndstopPin1VF.step]
2020-12-29 Add drawing and fix plate file
    [PlaqueBackVF.step, PlaqueFrontVF.step, PlateVF.step]
2020-12-30 Add version
    [SuperAntennaz Full Final Version.f3d, SuperAntennazFullV0.1.f3d, SuperAntennazFullV0.2.f3d]
2020-12-30 Change folder
    [Bracket.step, Endstop1.step, Endstop2.step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]
2020-12-31 Add version 0.3
    [Back Plate.step, Back_Plate.step, Bracket.step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]
2020-12-31 Add 3 and 5mm bracket
    [Back_Plate.dxf, Bracket5mm.step, Front_Plate.dxf]
2021-01-27 Add picture
    [Back Plate.step, Bracket.step, Fixatube.step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]
2021-01-28 Add V0.5
    [Back Plate.step, Bracket.step, Endstop Azimuth.step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]
2021-01-28 Add assembly instructions
2022-01-13 Add BOM for screws
    [SuperAntennaz Screws BOM.csv]
